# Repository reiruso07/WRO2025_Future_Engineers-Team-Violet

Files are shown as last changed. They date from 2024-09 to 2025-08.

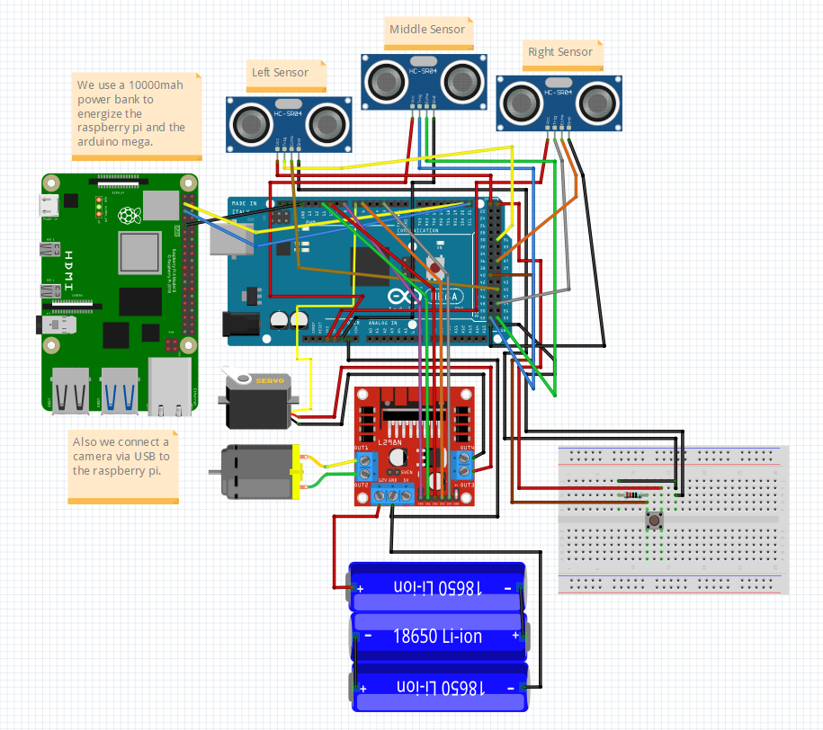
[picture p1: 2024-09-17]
schemes/scheme-structure/Full-Structure_Schematic.png

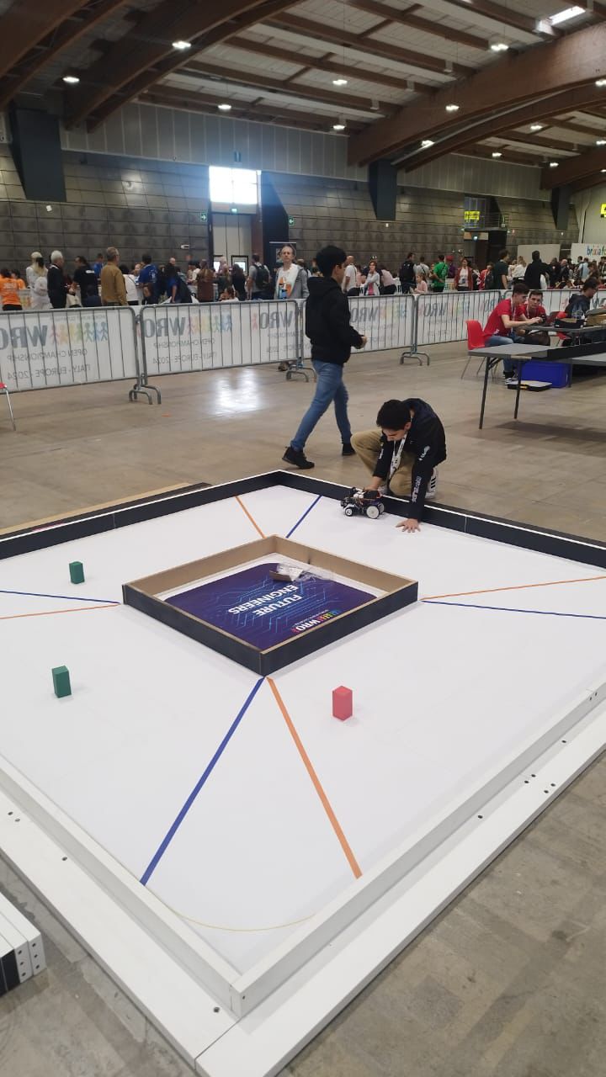
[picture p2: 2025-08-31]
t-photos/Our Journey/Italy_Competition_Test1.jpeg

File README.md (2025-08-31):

# Engineering Documentation - Team Violet 
Team Violet
## Introduction
In this repository you will find all the information related to the construction and assembly of the autonomous robot built by _Team Violet_ for the Future Engineers category in the 2025 Season.
This has been an incredible journey with a lot of obstacles, and we have done our best to come up with a design that we were not only satisfied with, but one that could properly acomplish all of the objectives present in this edition of the "Future Engineers" category.

## Contents
- [Team Violet's Members](https://github.com/reiruso07/WRO2025_Future_Engineers-Team-Violet/blob/main/README.md#team-violets-members)
- [Hardware Design](https://github.com/reiruso07/WRO2025_Future_Engineers-Team-Violet/blob/main/README.md#hardware-design)
   - [Design Process](https://github.com/reiruso07/WRO2025_Future_Engineers-Team-Violet/blob/main/README.md#design-process)
   - [Assembly Process](https://github.com/reiruso07/WRO2025_Future_Engineers-Team-Violet/blob/main/README.md#assembly-process)
   - [Elements](https://github.com/reiruso07/WRO2025_Future_Engineers-Team-Violet/blob/main/README.md#elements)
     - [3D Printed](https://github.com/reiruso07/WRO2025_Future_Engineers-Team-Violet/blob/main/README.md#3d-printed)
     - [Electronics](https://github.com/reiruso07/WRO2025_Future_Engineers-Team-Violet/blob/main/README.md#electronics)
- [Software Design](https://github.com/reiruso07/WRO2025_Future_Engineers-Team-Violet/blob/main/README.md#software-design)
   - [Image and Color Processing](https://github.com/reiruso07/WRO2025_Future_Engineers-Team-Violet/blob/main/README.md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)
     - [Image Capturing](https://github.com/reiruso07/WRO2025_Future_Engineers-Team-Violet/blob/main/README.md#image-capturing)
     - [Creating Red and Green masks](https://github.com/reiruso07/WRO2025_Future_Engineers-Team-Violet/blob/main/README.md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)
     - [Final Image](https://github.com/reiruso07/WRO2025_Future_Engineers-Team-Violet/blob/main/README.md#final-image)
     - [Distance from the cones](https://github.com/reiruso07/WRO2025_Future_Engineers-Team-Violet/blob/main/README.md#location-from-the-cones)
   - [Robot Movement](https://github.com/reiruso07/WRO2025_Future_Engineers-Team-Violet/blob/main/README.md#robot-movement)
     - [Smart Robot Servo configuration](https://github.com/reiruso07/WRO2025_Future_Engineers-Team-Violet/blob/main/README.md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)
     - [Robot Orientation](https://github.com/reiruso07/WRO2025_Future_Engineers-Team-Violet/blob/main/README.md#robot-orientation)
     - [Route Determination](https://github.com/reiruso07/WRO2025_Future_Engineers-Team-Violet/blob/main/README.md#route-determination)
   - [Data Sending](https://github.com/reiruso07/WRO2025_Future_Engineers-Team-Violet/blob/main/README.md#data-sending)
 - [Impact](https://github.com/reiruso07/WRO2025_Future_Engineers-Team-Violet/blob/main/README.md#impact)
 - [Our Journey](https://github.com/reiruso07/WRO2025_Future_Engineers-Team-Violet/blob/main/README.md#our-journey)

# Team Violet's Members
 - Adrian Alvarez:



>Hi, my name is Adrian Alvarez, I'm part of Team Violet and I'm responsible for the 3D designs used in the robot. My expectations of this competition are to learn and to test my skills in robotics.
 - Reinaldo Belmonte:



>My name is Reinaldo Belmonte. I am the team's programmer and I'm responsible for developing most (if not all) of the robot's moveset. My expectations for this season is to do my best with this project and, hopefully, end up in the first places.
 - Jose Zambrano:


   
>I am José Miguel Zambrano, the team's mechanic. I am in charge of the robot's assembly and its proper maintenance. For this season I hope, alongside my team, to deliver a project that meets the expectations, in addition to representing my institution and my country.

# Hardware Design
## Design Process
The robot is composed by a combination of 3D Printed parts for the most of its structure, the front wheels from a recicled toy car, the back wheels from a REV Robotics kit, and the electronics that give the robot its functionality.

Aditionally, the robot went through a multitude of changes until it reached its final iteration.
One of these changes was the replacement of the traditional DC motor that we used before with a «Hex Motor» , which provided a greater torque to the rear-wheel drive. 



As a result, the wheels used for the rear-wheel drive had to be also replaced, since the old ones couldn't adapt to the torque provided by the Hex Motor. This way we could take advantage of all the potential the Hex Motor had to offer.



Alongside the rear-wheel drive, we also made changes to the turning system, replacing the old Servomotor with a «Smart Robot Servo» , allowing for better and more precise turns when meeting a corner.



Another of these changes was the reorganization of its elements, given the changes in the motors used and the space they now occupied, we made a redistribution to most of the elements present in the robot, this time taking into account to make it even more accessible for repairs or adjustments to any of its parts.



The final design of the robot is intended as a modular design, consisting of 3 modules: lower «traction» module, middle «sensor processing» module, and upper «power supply and color processing» module. This makes it easier to make repairs on any of the modules or to replace or rearrange parts.



With all these changes made, a [3D design](https://github.com/reiruso07/WRO2024_Future_Engineers-Team-Violet/tree/main/other/model_structure) for the entire structure of the robot was made, thus facilitating its visualization and analysis.

## Assembly Process
The assembly process of the robot was divided into each module separately to later unify all the modules into a single robot. The assembly of the lower module started looking for different references on the internet to find an ideal location to place all the corresponding motors. After finding the ideal locations for each motor, the parts of the main chassis and the turning system were designed and 3D printed, tailored to each element to optimize the performance of the robot. 

Following this, we started the assembly of the second module, being much easier to carry out, since instead of using a 3d printed piece, we used a piece of compressed cardboard as a base to place all the elements of the second module. When performing this part of the assembly, we performed some functional tests to ensure that everything worked properly; there we realized that the HC-SR04 sensors suffered from detection failures due to how they were placed in the robot, so we designed an extension of the base to place them there, thus solving the problem.

Finally, we started the assembly of the 3rd and last module, following a sequence very similar to the previous one: We use a piece of compressed cardboard as the base of the 3rd module and place the corresponding elements.

And to unify the design, we drilled holes in the 3 bases of each module (except the main chassis which was already designed with these holes in mind) and joined them with multiple “pillar shafts” in a tower shape.

You can see the respective connections in the diagram below:

Team Violet (7)

## Elements
### 3D Printed
> [!NOTE]
> All of these pieces are printed in PLA plastic, with a thickness of 0.2mm and a filler level of between 20 to 50% (depends on the piece).

- **Main Chassis**: It's the piece that contains and supports all the components found in the robot.



- **Hex Motor Support Bracket**: A piece that helps fasten the Hex Motor to the Main Chassis structure.
  


- **Smart Robot Servo Support Bracket**: A piece that helps fasten the Servo Motor to the Main Chassis structure.



- **HC-SR04 Support Bracket**: Located in the "Bumper" piece, it serves as support for the HC-SR04 ultrasonic sensor, allowing it to function properly.
  


- **Bumper**: Used as a extension of the Main Chassis piece, it is used to locate the HC-SR04 sensors a little further ahead so it can detect the walls more easily.
  


- **Crossing System**: As it's name says, this part makes it possible to transmit the movement of the servomotor to the front wheels, thus allowing the robot to change direction.
  


- **Crossing System Support Piece**: The function of this piece is to join or support the two wheels, in other words, it is the one that produces a support point for them, which allows them to rotate on a fixed axle.



### Electronics
  -  **L298N Motor Driver**: Located in the middle module, it is used to manage the Hex Motor and provide both the Hex Motor and the Smart Robot Servo with energy.



> [!IMPORTANT]
> Specifications
>- Channels: 2 (supports 2 DC motors or 1 PAP motor)
>- Logic voltage: 5V.
>- Operating Voltage: 5V-35V.
>- Current consumption (Digital): 0 to 36mA.
>- Current capacity: 2A (peaks up to 3A).
>- Maximum power: 25W.
>- Weight: 30g.

  -  **Hex Motor**: Located in the lower module of the robot, this motor serves a rear wheel drive for the robot, providing the foward or backward motion of the robot.



> [!IMPORTANT]
>Specifications
>- Output Shaft: 5mm Female Hex
>- Weight: 199g.
>- Voltage: 12V DC
>- Free Speed: 125 RPM
>- Stall Torque: 3.2 N-m
>- Stall Current: 4.4 A
>- Gear Ratio: 72:1
>- Encoder Counts per Revolution
>- At the motor: 4 counts/revolution
>- At the output: 288 counts/revolution

  -   **Smart Robot Servo**: Located alongside the Hex Motor, it gives the robot the ability to rotate the front wheels, changing the orientation of the robot, thus allowing the robot to move freely in any direction on a flat surface.



> [!IMPORTANT]
>- Specifications
>- Weight: 58g.
>- Speed: 0.14 s/60° (at 6V)
>- Stall Torque: 13.5 kg-cm / 187.8 oz-in (at 6V)
>- Stall Current: 2A (at 6V)
>- Voltage Rating: 4.8V – 7.4V, 6V nominal
>- Input Pulse Range: 500μs – 2500μs
>- Default Angular Range: 270°
>- Maximum programmable range in angular mode: 280°
>- Gear Material: Metal
>- Spline type: 25T
>- Spline Internal Thread Size: M3
>- Spline Internal Thread Depth: 6mm

  -   **Arduino Mega 2560 R3**: Located in the middle module, it is used to manage the robot's mobility alongside the L298N Motor Driver, thus allowing the robot to move freely on a flat surface.



> [!IMPORTANT]
>- Microcontroller: ATmega2560
>- Input voltage: 7-12V.
>- 54 digital Input/Output pins (14 of them are PWM outputs).
>- 16 analog inputs.
>- 256k flash memory.
>- 16Mhz clock speed.

  -   **Raspberry Pi 4**: The Raspberry Pi 4 is a single-board development board used for entry-level computing. It is located in the upper module and it has the purpose of managing the "Color Processing" section, thus allowing the robot to recognize adjacent colors and use this information advantegiously.



> [!IMPORTANT]
>- Broadcom BCM2711, Quad core Cortex-A72 (ARM v8) 64-bit SoC @ 1.8GHz
>- 4GB LPDDR4-3200 SDRAM (depending on model)
>- 2.4 GHz and 5.0 GHz IEEE 802.11ac wireless, Bluetooth 5.0, BLE
>- Gigabit Ethernet
>- 2 USB 3.0 ports; 2 USB 2.0 ports.
>- 2 × micro-HDMI® ports (up to 4kp60 supported)
>- OpenGL ES 3.1, Vulkan 1.0
>- Micro-SD card slot for loading operating system and data storage
>- 5V DC via USB-C connector (minimum 3A*)
>- 5V DC via GPIO header (minimum 3A*)
>- Operating temperature: 0 – 50 degrees C ambient

   -   **HC-SR04 Ultrasonic Sensor**: The robot has 3 HC-SR04 ultrasonic sensors on the left, right and front of the "Bumper" piece, located in front of the middle module. They are used to provide orientation to the robot when moving in any environment, allowing it to detect obstacles or adjacent walls.



> [!IMPORTANT]
>- Supply voltage: 5 Vcc
>- Working frequency: 40 KHz
>- Maximum range: 4.5 m
>- Minimum range: 2.0 cm
>- Minimum trigger pulse duration (TTL level): 10 μS.
>- Duration of the output echo pulse (TTL level): 100-25000 μS.
>- Minimum waiting time between one measurement and the start of another: 20 mS.
  
   -   **Camera**: The robot uses an Spedal MF920P Webcam to recognize the colors in the environment. It has a Full HD 1080p resolution at 30 fps, with a H.264 Video Compression and a microphone incorporated.


   
   -   **3.7V 18650 Lithium Batteries**: Used to provide power to the Hex Motor and Smart Robot Servo on the lower module, this batteries have a nominal voltage of 3.7V and a maximum voltage of 4.2V and a capacity of 3500 mAh each.



   -   **LDNIO 10000mAh Power Bank**: We use a LDNIO 10000mAh Power Bank to supply Raspberry Pi and the Arduino Mega with energy. It has 1 USB ports, along with a Micro-USB port for charging, with an output voltage of 5V and 2.4A.



# Software Design
## Image and Color Processing
### Image Capturing
For color detection, the Spedal MF920P camera is used to capture a frame which is processed with Python thanks to the OpenCV image manipulation library.
### Creating Red and Green masks
OpenCV reads the images or frames in BGR, therefore it is necessary to transform them to the HSV color space. This is because the parameters that we are going to give to identify the colors work in the HSV model (Hue, Saturation, Value). To do this we will use the function `cv2.cvtColor`, as first argument we will give the image to transform, and then `cv2.COLOR_BGR2HSV`, to indicate that we will transform from BGR to HSV.
The parameters used to identify red were: 

    rojobajo1=np.array([0,150,20],np.uint8)

    rojoalto1=np.array([3,255,255],np.uint8)

    rojobajo2=np.array([175,100,20],np.uint8)

    rojoalto2=np.array([179,255,255],np.uint8)

and the parameters used for green were:
  
    verdebajo=np.array([35,100,20],np.uint8)

    verdealto=np.array([80,255,255],np.uint8)

The result of these procedures is a binary image in which the whites are the colors detected with the parameters given above. This image will be used later to obtain the final image.

Team Violet (1)

### Final Image
To obtain the final image we will use the functions `cv2.findContours` and `cv2.drawContours` from the OpenCV library. The function `cv2.findContours` is used to identify the colors detected in the binary image that together with the function `cv2.drawContours` is used to mark the obstacles in the final image.
### Location from the cones
To identify how far the cones are from the robot, the image is divided into four positions:

Team Violet (3)
1, 2, 3, and 4

The higher the position means that the obstacle is farther away from the robot, and with this information be able to calculate how much the robot has to move to avoid the cones more effectively.

## Robot Movement
### Smart Robot Servo configuration
The Smart Robot Servo is set on Pin 7 of the Arduino Mega and is configured with `Servo.write` function. The moveset of the Smart Robot Servo is defined by the distance given by the HC-SR04 sensors depending on whether the walls are near, far away or in a corner.
### Robot Orientation
The orientation of the robot is defined by the first corner, if the corner is of the rigth side it means that the direction is clockwise and 
vice versa.
### Route Determination
The determination of the routes is based on the color of the cone next to the robot. If the Python code detects a color this information will be sent to the arduino and transformed into a left or right turn depending on the detected color.

## Data Sending
First of all, we import the `smbus` library and then declare the `i2c identifier` that the Raspberry Pi 5 will have, additionally, the `i2c address` that the Raspberry Pi 5 has is placed, which is obtained thanks to a command executed in the terminal; then we create a function in charge of sending the information to the Arduino Mega 2560 R3 through an i2c connection that consist in three wires SDA (Serial Data Line), SCL (Serial Clock Line), and GND.

# Impact
The goal of this project is to evaluate the capabilities of the autonomous robot in fulfilling the various tasks that the competition demands. In the course of achieving these objectives, we had to develop a variety of skills to be able to meet all the objectives successfully, some of these skills being: the ability to analyze and correct errors in the programming of the project (both in the mobility section and in the color processing section), having to detect and correct these errors quickly in order to make progress in the expected completion times. Another of these skills was 3D design, which we used frequently to create different parts that were necessary to allow or facilitate the proper functioning of all components present in the robot.

The development of this project for the Future Engineers category was quite a journey to come up with a design that could stand up to the challenges we faced, and regardless of the outcome, it will be worth all the effort we made, since in the end, it made us grow.

# Our Journey
Our adventure in the WRO (World Robot Olympiad) began in 2023, when we were invited by our friends from Liceo Los Robles in Maracaibo. At first, it seemed like a simple task, but over time we discovered the true challenge of this competition, which has had a deep impact on us.

In 2024, we, José Miguel, Reinaldo, and Adrián joined forces in the Future Engineers category, embarking on a journey full of challenges and learning experiences. It was a roller coaster of emotions, with moments of triumph and frustration, but every second of effort has been worth it. The countless hours of work, discipline, and sacrifice have not only allowed us to grow in the field of robotics, but have also strengthened us as people. We have developed leadership, conflict resolution, decision-making, and, above all, a strong bond as a team.

2024 was a year of unforgettable achievements. We qualified for the national competition and, thanks to an invitation from Fundesteam Venezuela, we had the honor of participating in the WRO International Open in Brescia, Italy. Traveling to another continent to compete seemed like a dream, and we made it come true. We placed in an outstanding 4th place, just a few points behind the top spots. We were the only representatives from the Americas in our category and received a Gold mention for our performance, which placed us in first place in Latin America for the score achieved.
This experience filled us with pride and gratitude, but it also motivated us to seek new challenges in 2025. With a lot of effort, we have managed to qualify for the national finals among the top three teams. We are confident that our dedication and discipline will lead us to first place to represent Venezuela at the International Competition in Singapore.
Today, looking back, we feel immensely proud of how we have grown and overcome challenges together. We are ready to enjoy, cooperate, and give our best at this 2025 WRO National Competition.

--------------------------------------------------------------------------------------------------------------------------------------
Thank You. Team Violet - 2025.
======================================================================================================================================

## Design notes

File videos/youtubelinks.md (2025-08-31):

Team Violet (5)

## Demonstration Videos
### [- Standard Track, No Obstacles](https://youtu.be/GVMM1p4TWF8)
### [- Standard Track, Obstacles (Explanation)](https://youtu.be/eFcmwkvV04U)
### [- Standard Track, Obstacles 1](https://youtu.be/VMHjxnOMjBY)
### [- Standard Track, Obstacles 2](https://youtu.be/wLStcMTi5x4)
### [- Altered Track #1, No Obstacles](https://youtu.be/2meB4UbzeKI)
### [- Altered Track #2, No Obstacles](https://youtu.be/sTHwIlyS01U)
### [- Extra, How to cope with adversity](https://youtube.com/shorts/ftBgpBT6m5o?feature=share)

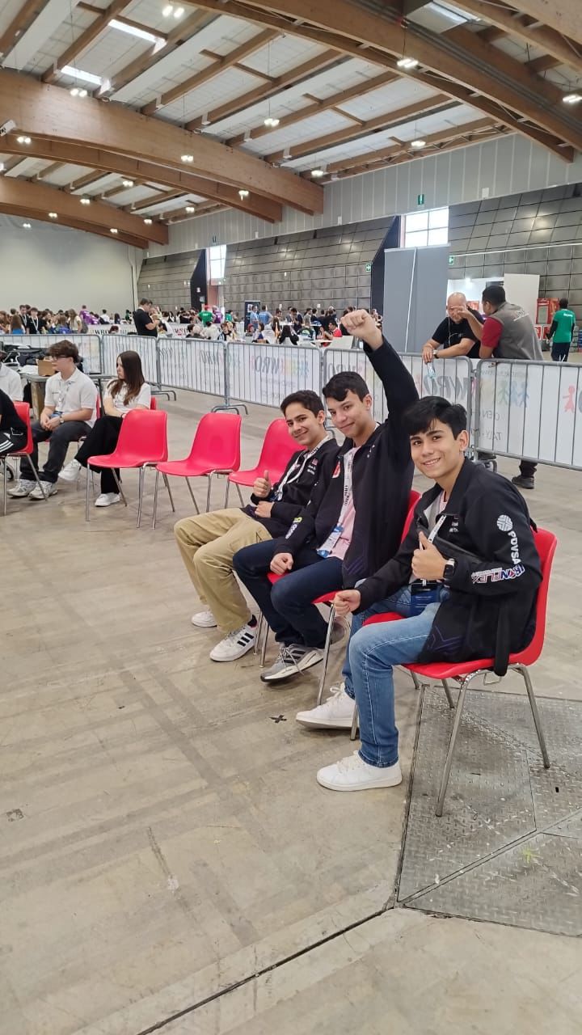
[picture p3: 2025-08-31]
t-photos/Our Journey/Italy_Competition1.jpeg

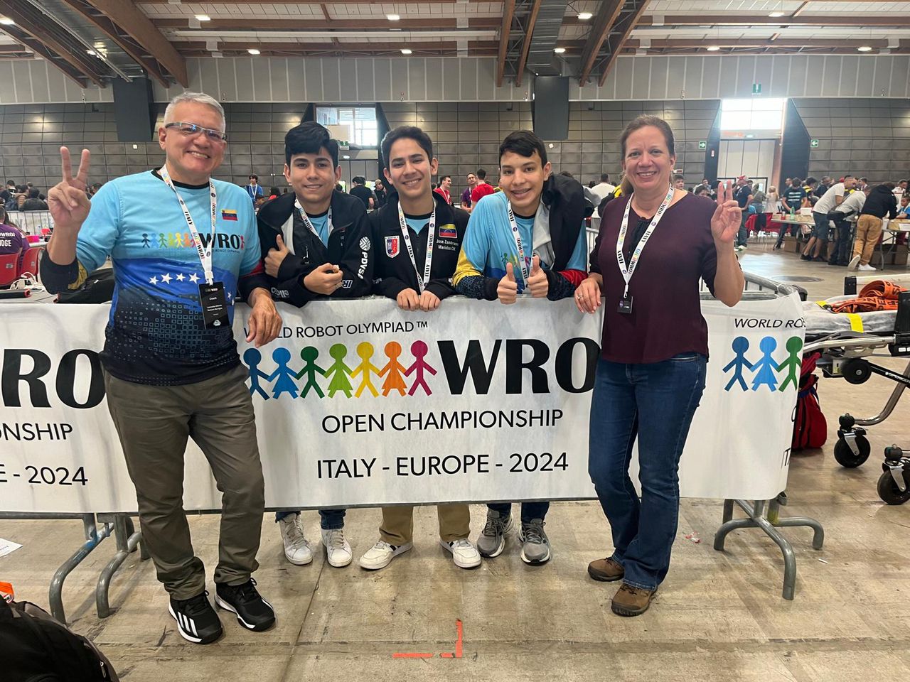
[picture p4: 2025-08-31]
t-photos/Our Journey/Italy_Competition3.jpeg

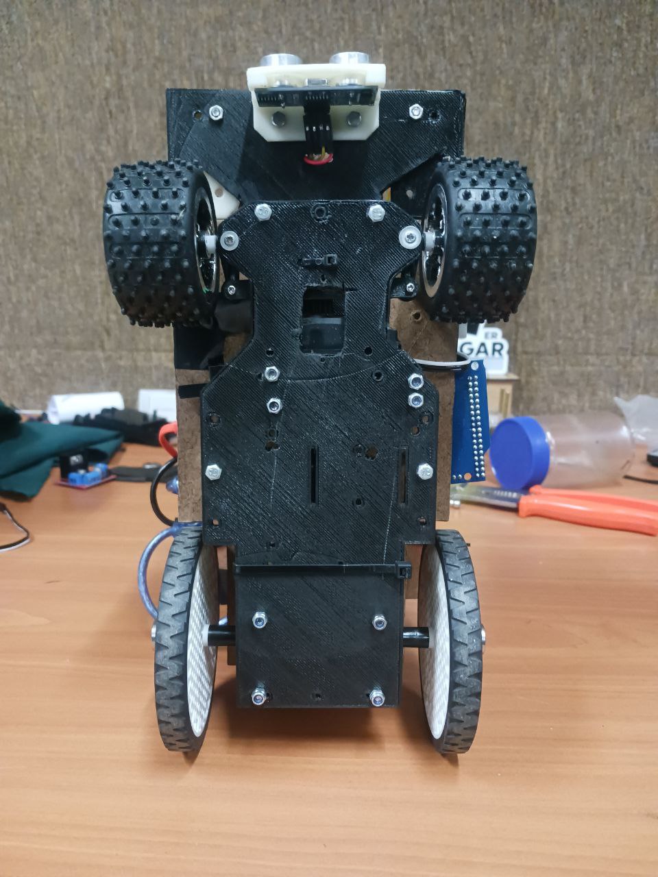
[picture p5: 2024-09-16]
v-photos/bottomview.jpg

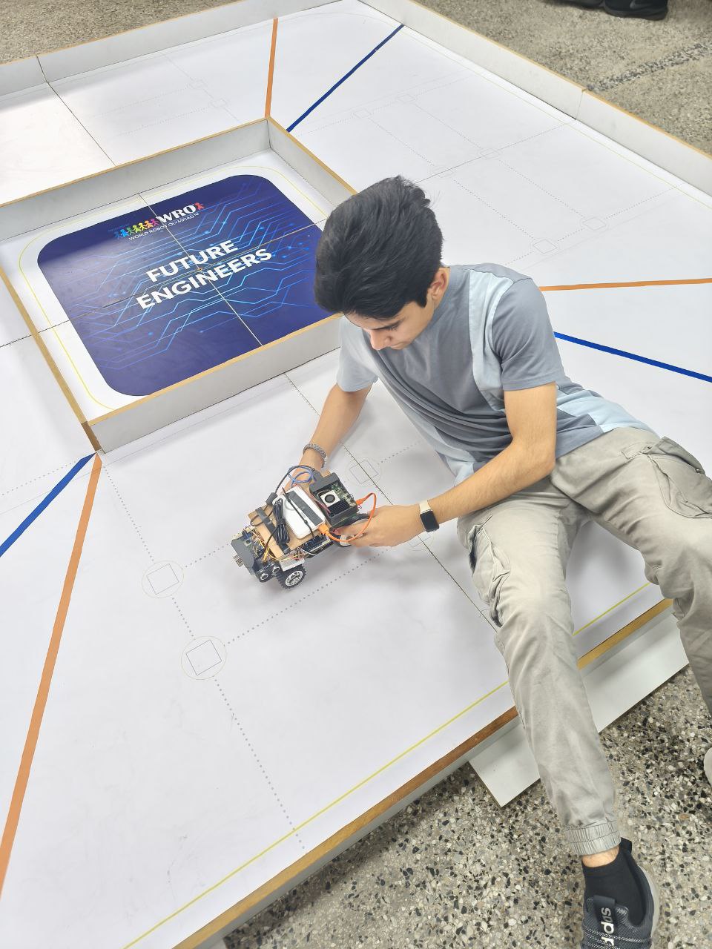
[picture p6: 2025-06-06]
t-photos/Teamwork/checking-robot.jpg

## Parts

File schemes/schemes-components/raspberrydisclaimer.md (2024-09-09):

> [!IMPORTANT]
> Since Raspberry Pi's are not "Open Hardware", and the 5 variant is so recent, we couldn't find the schematics for it. But we leave the Raspberry Pi 4 schematic since both have similar pinouts.

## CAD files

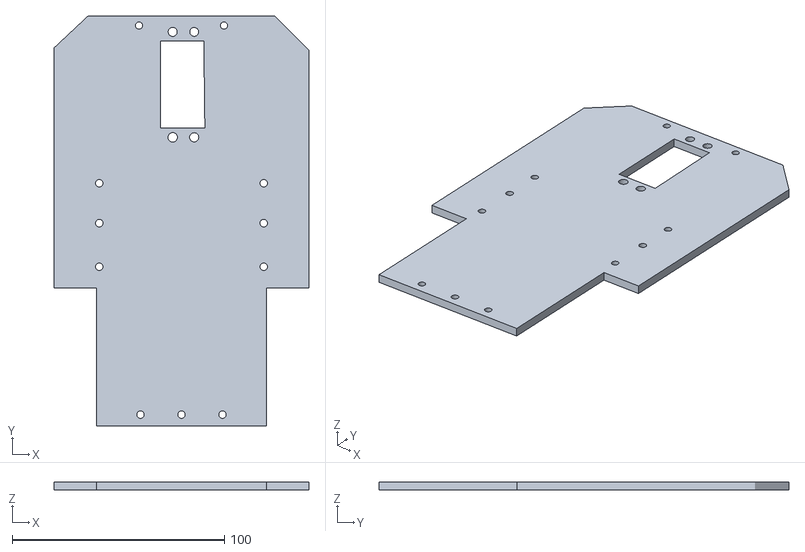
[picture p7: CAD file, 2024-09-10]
models/Main_Chassis_v1.stl
120.0 x 193.0 x 4.00

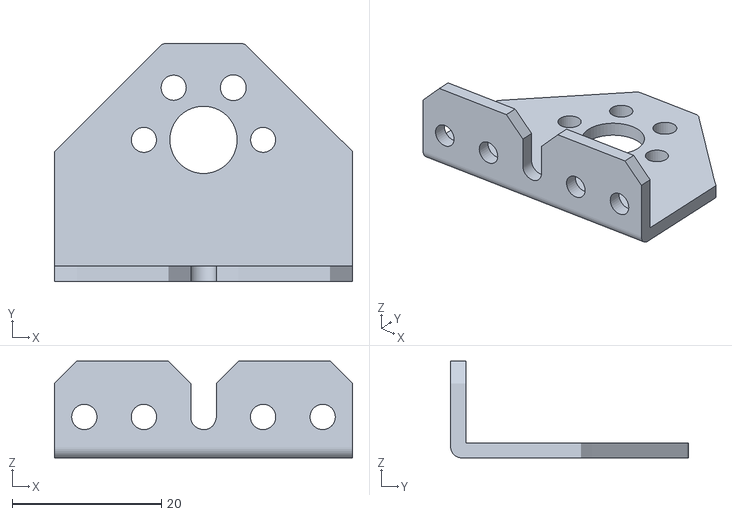
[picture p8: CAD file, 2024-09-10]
models/Core_Hex_Motor_Support_Bracket_v4.stl
40.0 x 31.9 x 13.0

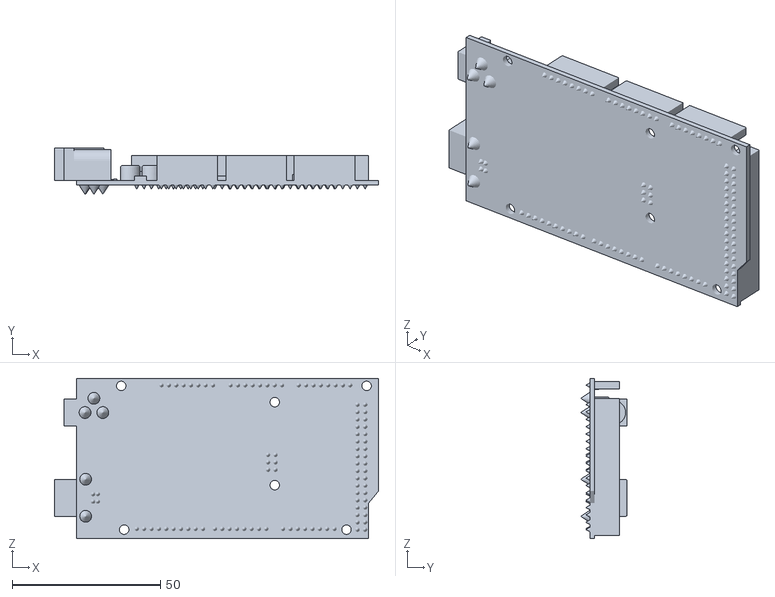
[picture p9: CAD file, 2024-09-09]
other/models-components/Arduino_Mega v1.stl
109.3 x 15.6 x 54.0

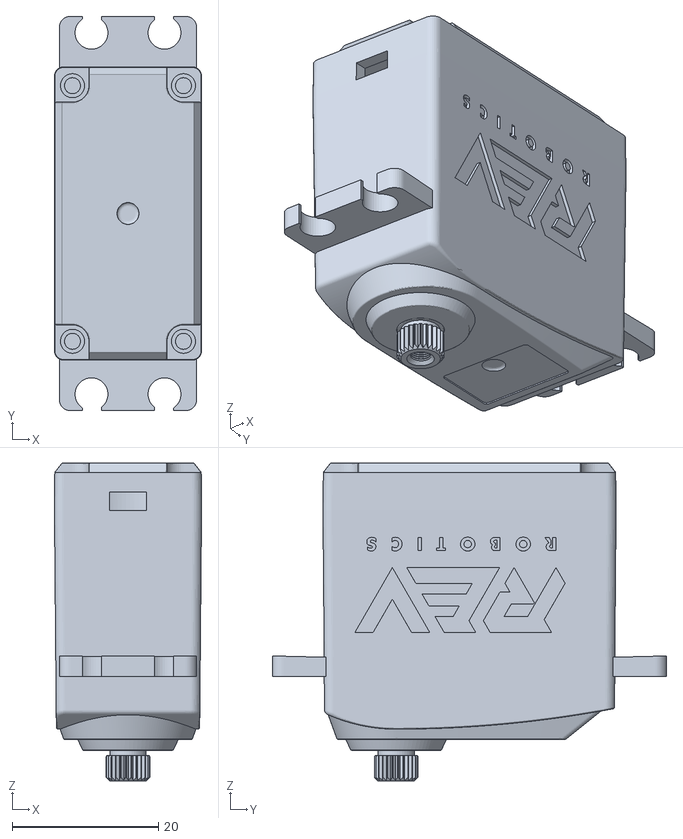
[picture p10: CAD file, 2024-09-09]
other/models-components/Smart Robot Servo.stl
20.2 x 54.0 x 43.5

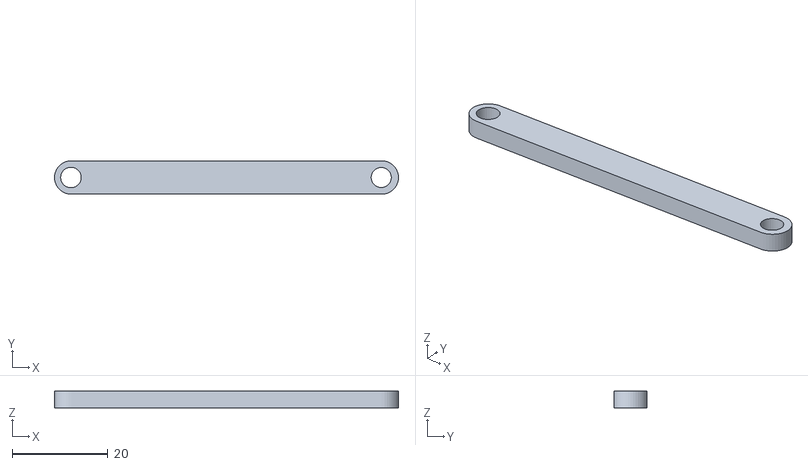
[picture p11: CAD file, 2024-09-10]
models/Crossing_Support_Piece_v2.1.stl
72.0 x 7.00 x 3.50

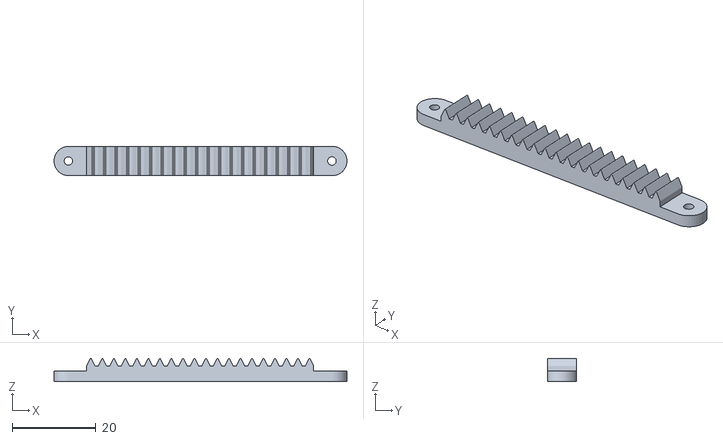
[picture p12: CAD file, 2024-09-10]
models/Crossing_System_Piece_v6.stl
70.0 x 7.00 x 5.56

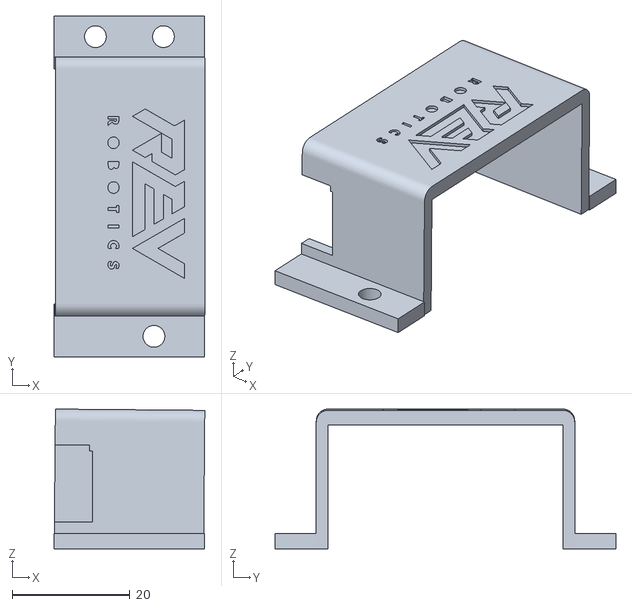
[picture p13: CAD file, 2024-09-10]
models/Smart_Servo_Support_Bracket_v2.stl
25.6 x 57.9 x 23.7

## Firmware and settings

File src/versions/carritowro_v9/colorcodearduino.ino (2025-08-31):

//Inclusion of Libraries
#include <Wire.h>
#include <Servo.h>
#include <L298N.h>
#include <NewPing.h>
//Variable declaration
#define IN2 10
#define IN1 11
#define IN3 6
#define IN4 3
#define I2C_DEVICE_ADDRESS 0x8
#define EN 8
String entradai2c="";
char te="";
int echo= 45;
int triger= 44;
int echo2=25;
int triger2=24;
int echo3=31;
int triger3=30;
int echo4=37;
int triger4=36;
int pulsador=40;
int maxd=450;
int atras=0;
int no=0;
int esq2=0,esq3=0;
int esqderatr=0;
int esquinadertrs=0;
int valorpulsador=0;
int esquinaderalt=0;
bool ra1,ra2,rm1,rm2,rm3,rm4,rm5,rm6,rm7,rm8,rm9,ra3,ra4,ra5,ra6,ra7,ra8,ra9,va1,va2,vm1,vm2,vm3,vm4,vm5,vm6,vm7,vm8,vm9,va3,va4,va5,va6,va7,va8,va9,rd1,rd2,rd3,rd4,rd5,rd6,rd7,rd8,rd9,vd1,vd2,vd3,vd4,vd5,vd6,vd7,vd8,vd9;
bool noconos,conorojoder,cnr,cnv;
int distanciaatr,distanciapasada;
int ciclo=0,vgn;
float distanciaade,distanciaizq,distanciader;
int cruzconorojo,cruzconorojoizq=0,cruzconorojoizq2=0,cruzconorojoizq3=0,cruzconorojonc=0,cruzconorojo2,cruzconoverde,cruzconoverde2=0,cuzconoverde3=0,cruzconoverdeizq,cruzconoverdeizq2=0,cuzconoverdeizq3=0;
int crucecono = 0,cruceconor2 = 0,cruceconocent=0,cruceconov=0,cruceconov2,cruceconovnc;
int esq=0;
int motors=1;
bool cnrojo=0,cnverde=0,rc=0,vc=0;
int lineas=0;
bool pared=0;
int paredizq=0;
int paredizqpeg=0;
int paredizqalt=0;
int paredder=0;
int paredderpeg=0;
int esquina=0,esquina2=0;
int esquinader=0,esquinader2=0,esquinader3=0;
bool esquinaderv=0,esquinaizqv=0;
bool esquinaizqr=0;
int pareder2=0;
int pared2=0;
int izq=0;
int der=0;
int esqc=0;
int si=0;
bool conorfin=0,conorcont=0,conovfin=0,conovcont=0,nc=0;
bool conorp=0,conovp=0,nconos;
int intervalocono = 1000,intervaloconov=1000;
int intervalodespuescono=1000;
const int intervalopared=200;
unsigned long cont;
unsigned long antespared=0;
unsigned long antesparedder=0;
unsigned long tiempoantesdelcont=0;
unsigned long tiempoantesdelcontder=0;
unsigned long valorantesconor = 0;
unsigned long valorantesconov = 0;
unsigned long valordespuesconor=0;
unsigned long valordespuesconov=0;
unsigned long contfincono=0,contfinconov=0;
unsigned long contnoconos=0;
int intervalo=2000;
int intervaloder=2200;
int esquinatrs=0;
//Motors and ultrasonics declaration
NewPing ultrasonidoade(triger,echo,maxd);
NewPing ultrasonidoder(triger3,echo3,maxd);
NewPing ultrasonidoizq(triger2,echo2,maxd);
NewPing ultrasonidoatr(triger4,echo4,maxd);
L298N motor(EN, IN2, IN1);
Servo servo;
void setup() {
  //Serial Monitor startup
  Serial.begin(115200);
  //I2c direction assignment
  Wire.begin(I2C_DEVICE_ADDRESS);
  Wire.onReceive(recibirm);
  Wire.onRequest(enviarM);
  //Servo pin assignment 
  servo.attach(39);
  //Definition of input and output pins
  pinMode(IN4, OUTPUT);
  pinMode(IN3, OUTPUT);
  pinMode(IN2, OUTPUT);
  pinMode(IN1, OUTPUT);
  pinMode(triger, OUTPUT);
  pinMode(echo, INPUT);
  pinMode(triger2, OUTPUT);
  pinMode(echo2, INPUT);
  pinMode(triger3, OUTPUT);
  pinMode(echo3, INPUT);
  pinMode(triger4, OUTPUT);
  pinMode(echo4, INPUT);
  pinMode(pulsador,INPUT_PULLUP);
  //Definition of motor speed
  motor.setSpeed(120);
  motor.stop();
  servo.write(90);
}
// principal loop start 
void loop() {
//Assignment of variable values
  cont = millis();
  distanciaade = ultrasonidoade.ping_cm();
  delay(30);
  distanciaizq = ultrasonidoizq.ping_cm();
  delay(30);
  distanciader = ultrasonidoder.ping_cm();
  delay(30);
  distanciaatr = ultrasonidoatr.ping_cm();
  if(lineas<12){
    digitalWrite(IN3,HIGH);
    digitalWrite(IN4,LOW);
  Serial.print("cont: ");
  Serial.println(cont);
  Serial.print("sensor adelante: ");
  Serial.println(distanciaade);
  Serial.print("sensor derecha: ");
  Serial.println(distanciader);
  Serial.print("sensor izquierda: ");
  Serial.println(distanciaizq);
  Serial.print("lineas");
  Serial.println(lineas);
  Serial.print("no: ");
  Serial.println(no);
  int centro=(distanciaizq+distanciader);
  if(motors==1){
    carrorect();
  }
  //Corner crossing conditions
  if((distanciaizq>100&&distanciaizq<300&&der==0&&izq==0&&distanciaade<=10&&si==0&&esquinadertrs==0&&esquinader==0&&esquinatrs==0)||esquina==1){
    if((cont-tiempoantesdelcont>intervalo)||esq==0){
      tiempoantesdelcont=cont;
      if(esq==0){
        noconos=0;
        ra1=0;
        ra2=0;
        ra3=0;
        ra4=0;
        ra5=0;
        ra6=0;
        ra7=0;
        ra8=0;
        ra9=0;
        rm1=0;
        rm2=0;
        rm3=0;
        rm4=0;
        rm5=0;
        rm6=0;
        rm7=0;
        rm8=0;
        rm9=0;
        rd1=0;
        rd2=0;
        rd3=0;
        rd4=0;
        rd5=0;
        rd6=0;
        rd7=0;
        rd8=0;
        rd9=0;
        va1=0;
        va2=0;
        va3=0;
        va4=0;
        va5=0;
        va6=0;
        va7=0;
        va8=0;
        va9=0;
        vm1=0;
        vm2=0;
        vm3=0;
        vm4=0;
        vm5=0;
        vm6=0;
        vm7=0;
        vm8=0;
        vm9=0;
        vd1=0;
        vd2=0;
        vd3=0;
        vd4=0;
        vd5=0;
        vd6=0;
        vd7=0;
        vd8=0;
        vd9=0;
        esquina=1;
        carrorect();
        stopcar();
        intervalo=1800;
        si=1;
        esq=1;
        servo.write(35);
        motor.backward(); 
        izq=1;
        motors=0;
      }
       else if(esq==1){
       stopcar();
       servo.write(85);
       motor.stop();
       motor.forward();
       intervalo=600;
       esq=2;
      }
      else if(esq==2){
        
       stopcar();
       servo.write(85);
       motor.stop();
       no=1;
       if(no==0){
          no=1;
       }
        intervalo=1000;
       esq=3;
      }
       else if(esq==3){
        carrorect();
        motors=1;
        lineas++;
        esquina=0;
        no=0;
        izq=1;
        enviarM();
        tiempoantesdelcont=0;
        esq=0;if(ra1==0&&ra2==0&&rm1==0&&rm2==0&&rd1==0&&rd2==0&&va1==0&&va2==0&&vm1==0&&vm2==0&&vd1==0&&vd2==0){
          noconos=1;
        }
        else{
          noconos=0;
        }
       }
       
  }
  }
 //Initial turn
if((distanciader>100&&esquina==0&&distanciaade<=15&&izq==0&&der==0&&si==0)||esquinader==1){
    if((cont-tiempoantesdelcont>intervaloder)||esq3==0){
      tiempoantesdelcont=cont;
      if(esq3==0){
        noconos=0;
        ra1=0;
        ra2=0;
        rm1=0;
        rm2=0;
        rd1=0;
        rd2=0;
        va1=0;
        va2=0;
        vm1=0;
        vm2=0;
        vd1=0;
        vd2=0;
        esquinader=1;
        carrorect();
        stopcar();
        intervaloder=1700;
        si=1;
        esq3=1;
        servo.write(140);
        motor.backward(); 
        der=1;
        motors=0;
      }
      else if(esq3==1){
        
       stopcar();
       servo.write(85);
       motor.stop();
       motor.forward();
       intervaloder=600;
       esq3=2;
      }
      else if(esq3==2){
        
       stopcar();
       servo.write(85);
       motor.stop();
       no=1;
       if(no==0){
          no=1;
       }
        intervaloder=1200;
       esq3=3;
      }
      else if(esq3==3){
        carrorect();
        motors=1;
        esq3=0;
        lineas++;
        no=0;
        if(no==1){
          no=0;
        }
        intervaloder=1000;
        esquinader=0;
        tiempoantesdelcont=0;
        si=1;
        enviarM();
        if(ra1==0&&ra2==0&&rm1==0&&rm2==0&&rd1==0&&rd2==0&&va1==0&&va2==0&&vm1==0&&vm2==0&&vd1==0&&vd2==0){
          noconos=1;
        }
        else{
          noconos=0;
        }
      }   
    }     
  }
  if((distanciader>100&&esquinadertrs==0&&esquinader3==0&&esquina==0&&distanciaade<=15&&izq==0&&der==1&&si==0&&cruzconorojo2==0&&conorfin==1&&conovfin==0)||esquinaderalt==1){
    Serial.println("esquina despues de esquivar cono rojo");
   if((cont-tiempoantesdelcont)>intervaloder||esq==0){
    tiempoantesdelcont=cont;
   Serial.println(tiempoantesdelcont); 
    if(esq==0){
      noconos=0;
        ra1=0;
        ra2=0;
        rm1=0;
        rm2=0;
        rd1=0;
        rd2=0;
        va1=0;
        va2=0;
        vm1=0;
        vm2=0;
        vd1=0;
        vd2=0;
        Serial.println("Hola");
        esquinaderalt=1;
        carrorect();
        stopcar();
        intervaloder=1900;
        si=1;
        esq=1;
        servo.write(140);
        motor.backward();
        motors=0;
      }
      else if(esq==1){
        no=1;
        if(no==0){
          no=1;
        }
       stopcar();
       servo.write(85);
       motor.stop();
        intervaloder=1200;
       esq=2;
      }
      else if(esq==2){
        carrorect();
        motors=1;
        esq=0;
        lineas++;
        no=0;
        intervaloder=1000;
        esquinaderalt=0;
        tiempoantesdelcont=0;
        enviarM();
        conorfin=0;
        if(ra1==0&&ra2==0&&rm1==0&&rm2==0&&rd1==0&&rd2==0&&va1==0&&va2==0&&vm1==0&&vm2==0&&vd1==0&&vd2==0){
          noconos=1;
        }
        else{
          noconos=0;
        }
      }   
        
   }
  }
  if((distanciader>100&&distanciaade<=36&&izq==0&&der==1&&si==0&&cruzconorojo2==0&&conovfin==1&&conorfin==0)||esquinaderv==1){
   if((cont-tiempoantesdelcont)>intervaloder||esq==0){
    tiempoantesdelcont=cont;
    if(esq==0){
      noconos=0;
        ra1=0;
        ra2=0;
        rm1=0;
        rm2=0;
        rd1=0;
        rd2=0;
        va1=0;
        va2=0;
        vm1=0;
        vm2=0;
        vd1=0;
        vd2=0;
        esquinaderv=1;
        carrorect();
        stopcar();
        intervaloder=1200;
        si=1;
        esq=1;
        servo.write(85);
       motor.backward();
        motors=0;
      }
      
      else if(esq==1){
       stopcar();
       
       servo.write(30);
        motor.forward();
        intervaloder=1800;
       esq=2;
      }
      else if(esq==2){
        no=1;
        if(no==0){
          no=1;
        }
        
       stopcar();
       no=1;
       servo.write(85);
       motor.stop();
        intervaloder=1200;
       esq=3;
      }
      else if(esq==3){
        carrorect();
        motors=1;
        esq=0;
        lineas++;
        no=0;
        intervaloder=1000;
        esquinaderv=0;
        tiempoantesdelcont=0;
        enviarM();
        conovp=0;
        conorp=0;
        conovfin=0;
        if(ra1==0&&ra2==0&&rm1==0&&rm2==0&&rd1==0&&rd2==0&&va1==0&&va2==0&&vm1==0&&vm2==0&&vd1==0&&vd2==0){
          noconos=1;
        }
        else{
          noconos=0;
        }
      }   
        
   }
  }
  if((distanciaizq>100&&distanciaade<=15&&izq==1&&der==0&&si==0&&cruzconorojo2==0&&conorfin==1&&conovfin==0)||esquinaizqr==1){
    tiempoantesdelcont=cont;
    if(esq==0){
      noconos=0;
        ra1=0;
        ra2=0;
        rm1=0;
        rm2=0;
        rd1=0;
        rd2=0;
        va1=0;
        va2=0;
        vm1=0;
        vm2=0;
        vd1=0;
        vd2=0;
        esquinaizqr=1;
        carrorect();
        stopcar();
        intervaloder=1800;
        si=1;
        esq=1;
        servo.write(85);
       motor.backward();
        motors=0;
      }
      
      else if(esq==1){
       stopcar();
       
       servo.write(140);
        motor.forward();
        intervaloder=1600;
       esq=2;
      }
      else if(esq==2){
       stopcar();
       no=1;
       servo.write(85);
       motor.backward();
        intervaloder=600;
       esq=3;
      }
      else if(esq==3){
        no=1;
        if(no==0){
          no=1;
        }
        Serial.println("se detuvo");
       stopcar();
       no=1;
       servo.write(85);
       motor.stop();
        intervaloder=1200;
       esq=4;
      }
      else if(esq==4){
        carrorect();
        motors=1;
        esq=0;
        lineas++;
        no=0;
        intervaloder=1000;
        esquinaizqr=0;
        tiempoantesdelcont=0;
        enviarM();
        conorfin=0;
        conovp=0;
        conorp=0;
        if(ra1==0&&ra2==0&&rm1==0&&rm2==0&&rd1==0&&rd2==0&&va1==0&&va2==0&&vm1==0&&vm2==0&&vd1==0&&vd2==0){
          noconos=1;
        }
        else{
          noconos=0;
        }
      }   
        
   }
  }
  if((distanciaizq>100&&esquinadertrs==0&&esquinader3==0&&esquina==0&&distanciaade<=15&&izq==1&&der==0&&si==0&&cruzconorojo2==0&&conovfin==1&&conorfin==0)||esquinaizqv==1){
    Serial.println("esquina despues de esquivar cono verde anti horario");
   if((cont-tiempoantesdelcont)>intervaloder||esq==0){
    tiempoantesdelcont=cont;
   Serial.println(tiempoantesdelcont); 
    if(esq==0){
      noconos=0;
        ra1=0;
        ra2=0;
        rm1=0;
        rm2=0;
        rd1=0;
        rd2=0;
        va1=0;
        va2=0;
        vm1=0;
        vm2=0;
        vd1=0;
        vd2=0;
        Serial.println("Hola");
        esquinaizqv=1;
        carrorect();
        stopcar();
        intervaloder=1700;
        si=1;
        esq=1;
        servo.write(30);
        motor.backward();
        motors=0;
      }
      
      else if(esq==1){
       stopcar();
       servo.write(85);
       motor.backward();
        intervaloder=300;
       esq=2;
      }
      else if(esq==2){
       stopcar();
       no=1;
       if(no==0){
        no=1;
       }
       servo.write(85);
       motor.stop();
        intervaloder=1200;
       esq=3;
      }
      else if(esq==3){
        carrorect();
        motors=1;
        esq=0;
        lineas++;
        no=0;
        intervaloder=1000;
        esquinaizqv=0;
        tiempoantesdelcont=0;
        enviarM();
        conovfin=0;
        if(ra1==0&&ra2==0&&rm1==0&&rm2==0&&rd1==0&&rd2==0&&va1==0&&va2==0&&vm1==0&&vm2==0&&vd1==0&&vd2==0){
          noconos=1;
        }
        else{
          noconos=0;
        }
      }   
        
   }
  }
  //Obstacle avoiding conditions
  if((((ra1!=0||ra2!=0)||cruzconorojoizq==1)&&der==0&&izq==1)&&esquinaizqr==0&&esquinaizqv==0&&esquinaderv==0&&esquina==0&&esquina2==0&&esq==0){
    Serial.println("cono rojo izq");
    noconos=0;
    if((((cont-valorantesconor)>intervalocono)||crucecono==0)&&cnrojo==0){
      valorantesconor=cont;
      if(crucecono==0){
          intervalocono=900;
          Serial.println("Hola b1");
         crucecono=1;
        cruzconorojoizq=1;
        carroesqder();
        motors=0;
        
        }
        else if(crucecono==1){
          Serial.println("Hola b2");
         crucecono=2;
         motor.stop();
         carroesqizq();
         intervalocono=1000;
        }
        else if(crucecono==2){
          Serial.println("Hola b3");
        crucecono=0;
        carrorect();
        valorantesconor=0;
        intervalocono=900;
        cnrojo=1;
        if(cnrojo==0){
          cnrojo=1;
        }
        crucecono=0;
        
        }
    }
    if(cnrojo==1){
      Serial.println("mantenerse derecho");
      
     if(((((cont-contfincono)>=1000)&&conorcont==1)||rc==1)&&cnr==0){
          Serial.println("centrar adios cono 3");
          
          if(((cont-valordespuesconor)>intervalodespuescono)||vgn==0){
            Serial.println("Hola mundo");
            valordespuesconor=cont;
        if(vgn==0){
          carrorect();
          motor.stop();
          no=1;
          rc=1;
          vgn=1;
          ciclo=1;
          
        }
        else if(vgn==1&&(vd1!=0||vd2!=0)){
          Serial.println("pp");
          no=0;
          cruzconorojoizq=0;
          crucecono=0;
          ra1=0;
          ra2=0;
          cnrojo=0;
          conorcont=0;
          valordespuesconor=0;
          vgn=0;
          rc=0;
          conorp=1;
          conorfin=0;
        }
        else if(vgn==1&&(vd1==0&&vd2==0)){
          Serial.println("ii");
          carrorect();
          cnr=1;
          conorcont=0;
          valordespuesconor=0;
          conorp=0;
          conorcont=0;
          no=0;
          ciclo=0;
        }
        
     }
    
     
    }
  
     else if(distanciaade<=100&&(((cont-contfincono)>=1000)&&conorcont==1)&&cnr==1){
      carrorect();
        cruzconorojoizq=0;
        crucecono=0;
        ra1=0;
        ra2=0;
        ra3=0;
        ra4=0;
        ra5=0;
        ra6=0;
        ra7=0;
        ra8=0;
        ra9=0;
        rm1=0;
        rm2=0;
        rm3=0;
        rm4=0;
        rm5=0;
        rm6=0;
        rm7=0;
        rm8=0;
        rm9=0;
        rd1=0;
        rd2=0;
        rd3=0;
        rd4=0;
        rd5=0;
        rd6=0;
        rd7=0;
        rd8=0;
        rd9=0;
        motors=1;
        cnrojo=0;
        conorfin=1;
        conorp=1;
        conorcont=0;
        rc=0;
        si=0;
     }
     else{
      if(conorcont==0){
        Serial.println("cont activated");
        contfincono=cont;
        conorcont=1;
      }
       conorojo();
        motors=0;
     }
    }
  }
  if((((rd1!=0||rd2!=0)||cruzconorojonc==1)&&der==0&&izq==1&&nc==1)&&esquinaizqr==0&&esquinaizqv==0&&esquinaderv==0&&esquina==0&&esquina2==0&&esq==0){
    noconos=0;
    if((((cont-valorantesconor)>intervalocono)||crucecono==0)&&cnrojo==0){
      valorantesconor=cont;
      if(crucecono==0){
          intervalocono=900;
         crucecono=1;
        cruzconorojonc=1;
        carroesqder();
        motors=0;
        
        }
        else if(crucecono==1){
         crucecono=2;
         motor.stop();
         carroesqizq();
         intervalocono=1100;
        }
        else if(crucecono==2){
        crucecono=0;
        carrorect();
        valorantesconor=0;
        intervalocono=900;
        cnrojo=1;
        nc=0;
        ciclo=0;
        si=0;
        cruzconorojonc=0;
        conorfin=1;
        rd1=0;
        rd2=0;
        rd3=0;
        rd4=0;
        rd5=0;
        rd6=0;
        rd7=0;
        rd8=0;
        rd9=0;
        if(cnrojo==0){
          cnrojo=1;
        }
        crucecono=0;
        
        }
    }
  }
    if((((rm1!=0||rm2!=0)||cruzconorojo2==1)&&der==0&&izq==1)&&esquinaizqr==0&&esquinaizqv==0&&esquinaderalt==0&&esquinaderv==0&&esquina==0&&va2==0&&va1==0&&ra2==0&&ra1==0){
    noconos=0;
    if((((cont-valorantesconor)>intervalocono)||cruceconocent==0)&&cnrojo==0){
      valorantesconor=cont;
      if(cruceconocent==0){
          intervalocono=1000;
         cruceconocent=1;
        cruzconorojo2=1;
        carroesqder();
        motors=0;
        }
        else if(cruceconocent==1){
          motors=0;
         cruceconocent=2;
         motor.stop();
         servo.write(145);
         motor.forward();
         valorantesconor=cont;
         intervalocono=1000;
        }
        else if(cruceconocent==2){
        cruceconocent=0;
        carrorect();
        valorantesconor=0;
        intervalocono=800;
        cnrojo=1;
        crucecono=0;
        conorfin=1;
        
        }
    }
    if(cnrojo==1){
      
     if((distanciaade<=100&&((cont-contfincono)>=2000)&&conorcont==1)){
        carrorect();
        cruzconorojo2=0;
        crucecono=0;
        cruceconocent=0;
        rm1=0;
        rm2=0;
        rm3=0;
        rm4=0;
        rm5=0;
        rm6=0;
        rm7=0;
        rm8=0;
        rm9=0;
        motors=1;
        cnrojo=0;
        conorfin=1;
        paredder=0;
       pareder2=0;
       motors=1;
       paredizq=0;
      si=0;
      pared2=0;
      conorcont=0;
     }
     else{
      if(conorcont==0){
        contfincono=cont;
        conorcont=1;
      }
       conorojo();
        motors=0;
     }
    }
  }
  else if((rm1!=0||rm2!=0)&&vd1==1||vd2==1||va1==1||va2==1||ra2==1||ra1==1||rd1==1||rd2==1){
    rm1=0;
        rm2=0;
        cruzconorojo2=0;
  }
  if((((rd1!=0||rd2!=0)||cruzconorojoizq3==1)&&der==0&&izq==1&&conovp==1)&&esquinader==0&&esquinader2==0&&esquinaderalt==0&&esquinaderv==0){
    noconos=0;
    if((((cont-valorantesconor)>intervalocono)||cruceconor2==0)){
      valorantesconor=cont;
      if(cruceconor2==0){
          intervalocono=1200;
         cruzconorojoizq3=1;
         cruceconor2=1;
        carroesqder();
        motors=0;
        }
        else if(cruceconor2==1){
          motors=0;
         cruceconor2=2;
         motor.stop();
         carrorect();
         servo.write(145);
         intervalocono=1500;
        }
        else if(cruceconor2==2){
        carrorect();
        valorantesconor=0;
        cruceconor2=0;
        intervalocono=1500;
        cruzconorojoizq3=0;
        conorfin=1;
        rd1=0;
        rd2=0;
        rd3=0;
        rd4=0;
        rd5=0;
        rd6=0;
        rd7=0;
        rd8=0;
        rd9=0;
        ciclo=0;
        si=0;
        }
    }
  }
  //Red obstacle in front
  if((((ra1!=0||ra2!=0)||cruzconorojo==1)&&der==1&&izq==0&&conorp==0)&&esquinader==0&&esquinader2==0&&esquinaderalt==0&&esquinaderv==0&&esquina==0&&esquina2==0){
    noconos=0;
    if((((cont-valorantesconor)>intervalocono)||crucecono==0)&&cnrojo==0){
      valorantesconor=cont;
      if(crucecono==0){
          intervalocono=900;
         crucecono=1;
        cruzconorojo=1;
        carroesqder();
        motors=0;
        }
        else if(crucecono==1){
         crucecono=2;
         motor.stop();
         carroesqizq();
         intervalocono=900;
        }
        else if(crucecono==2){
        crucecono=0;
        carrorect();
        valorantesconor=0;
        intervalocono=900;
        cnrojo=1;
        if(cnrojo==0){
          cnrojo=1;
        }
        crucecono=0;
        }
        
    }
    if(cnrojo==1){
      
     if(((((cont-contfincono)>=1500)&&conorcont==1)||rc==1)&&cnr==0){
          
          if(((cont-valordespuesconor)>intervalodespuescono)||vgn==0){
            valordespuesconor=cont;
        if(vgn==0){
          carrorect();
          motor.stop();
          no=1;
          rc=1;
          
          vgn=1;
          ciclo=1;
        }
        else if(vgn==1&&(vd1!=0||vd2!=0)){
          no=0;
          cruzconorojo=0;
          crucecono=0;
          ra1=0;
          ra2=0;
          cnrojo=0;
          conorcont=0;
          valordespuesconor=0;
          vgn=0;
          rc=0;
          conorp=1;
          conorcont=0;
          conorfin=0;
        }
        else if(vgn==1&&(vd1==0&&vd2==0)){
          carrorect();
          cnr=1;
          conorcont=0;
          valordespuesconor=0;
          conorp=0;
          conorcont=0;
          no=0;
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

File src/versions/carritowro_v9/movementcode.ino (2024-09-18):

//Inclusion of Libraries
#include <Servo.h>
#include <L298N.h>
#include <NewPing.h>
//Variable declaration
int IN2= 10;
int IN1= 11;
int IN3= 6;
int IN4= 3;
int EN= 8;
int echo= 53;
int triger= 52;
int echo2=45;
int triger2=31;
int echo3=37;
int triger3=49;
int buzz=11;
int maxd=450;
int atras=0;
int no=0;
int esq2=0;
int esqderatr=0;
int esquinadertrs=0;
int esquina=0;
int esq=0;
int motors=1;
int lineas=0;
bool pared=0;
int paredizq=0;
int paredizqpeg=0;
int paredizqalt=0;
int paredder=0;
int paredderpeg=0;
int paredderalt=0;
bool pareder=0;
int esquinader=0;
int pareder2=0;
int pared2=0;
int izq=0;
int der=0;
int si=0;
const int intervalopared=200;
unsigned long antespared=0;
unsigned long antesparedder=0;
unsigned long tiempoantesdelcont=0;
unsigned long tiempoantesdelcontder=0;
const  int intervalo=2000;
const int intervaloatr=1850;
const int intervaloder=1900;
const int intervaloderatr=1800;
int esquinatrs=0;
//Motors and ultrasonic declaration
Servo servo;
NewPing ultrasonidoade(triger,echo,maxd);
NewPing ultrasonidoder(triger3,echo3,maxd);
NewPing ultrasonidoizq(triger2,echo2,maxd);
L298N motor(EN, IN2, IN1);

void setup() {
  //Serial monitor startup
  Serial.begin(9600);
  //Servo pin assignment
  servo.attach(7);
  //Definition of input and output pins
  pinMode(IN4, OUTPUT);
  pinMode(IN3, OUTPUT);
  pinMode(IN2, OUTPUT);
  pinMode(IN1, OUTPUT);
  pinMode(triger, OUTPUT);
  pinMode(echo, INPUT);
  pinMode(triger2, OUTPUT);
  pinMode(echo2, INPUT);
  pinMode(triger3, OUTPUT);
  pinMode(echo3, INPUT);
  pinMode(buzz,OUTPUT);
  //Definition of motor speed
  motor.setSpeed(120);
  motor.stop();
  servo.write(90);
  
}

void loop() {
  //Loop start
  if(lineas<12){
    digitalWrite(IN3,HIGH);
    digitalWrite(IN4,LOW);
  //Assignment of variable values
  unsigned long cont = millis();
  float distanciaade = ultrasonidoade.ping_cm();
  float distanciaizq = ultrasonidoizq.ping_cm();
  float distanciader = ultrasonidoder.ping_cm();

  }
  if(motors==1){
    carrorect();
  }
//Corner crossing conditions
if((distanciaizq>100&&distanciaizq<300&&der==0&&izq==0&&si==0&&no==0&&esquinadertrs==0&&esquinader==0&&esquinatrs==0&&distanciaade>50&&distanciaade<80)||esquina==1){
    if((cont-tiempoantesdelcont>intervalo)||esq==0){
      tiempoantesdelcont=cont;
      if(esq==0&&esquinadertrs==0){
        esquina=1;
        si=1;
        no=1;
        esq=1;
        carroesqizq();
        motors=0;
        izq=1;
      }
      else{
        esq=0;
        carrorect();
        esquina=0;
        motors=1;
        lineas++;
        tiempoantesdelcont=0;
      }
    }
  }
if((distanciaizq>100&&distanciaizq<300&&izq==1&&der==0&&si==0&&no==0&&esquinadertrs==0&&esquinader==0&&esquinatrs==0&&distanciaade>50&&distanciaade<80)||esquina==1){
    if((cont-tiempoantesdelcont>intervalo)||esq==0){
      tiempoantesdelcont=cont;
      if(esq==0&&esquinadertrs==0){
        esquina=1;
        si=1;
        no=1;
        esq=1;
        carroesqizq();
        motors=0;
        izq=1;
      }
      else{
        esq=0;
        carrorect();
        esquina=0;
        motors=1;
        lineas++;
        tiempoantesdelcont=0;
      }
    }
  }
if((distanciaizq>=100&&distanciaizq<=300&&esquinadertrs==0&&esquinader==0&&esquina==0&&izq==0&&der==0&&si==0&&no==0&&distanciaade<=50)||esquinatrs==1){
    if((cont-tiempoantesdelcont>intervaloatr)||esq2==0){
      tiempoantesdelcont=cont;
      if(esq2==0&&esquinadertrs==0){
        esquinatrs=1;
        si=1;
        esq2=1;
        carroesqizq2();
        motors=0;
        izq=1;
        no=1;
      }
      else if(esq2==1&&esquinadertrs==0){
        esq2=0;
        carrorect();
        esquinatrs=0;
        motors=1;
        lineas++;
        tiempoantesdelcont=0;
      }
    }
  } 
if((distanciaizq>=100&&distanciaizq<=300&&esquinadertrs==0&&esquinader==0&&esquina==0&&izq==1&&der==0&&si==0&&no==0&&distanciaade<=50)||esquinatrs==1){
    if((cont-tiempoantesdelcont>intervaloatr)||esq2==0){
      tiempoantesdelcont=cont;
      if(esq2==0&&esquinadertrs==0){
        esquinatrs=1;
        si=1;
        esq2=1;
        carroesqizq2();
        motors=0;
        izq=1;
        no=1;
      }
      else if(esq2==1&&esquinadertrs==0){
        esq2=0;
        carrorect();
        esquinatrs=0;
        motors=1;
        lineas++;
        tiempoantesdelcont=0;
      }
    }
  } 
if((distanciader>100&&distanciader<300&&esquinadertrs==0&&esquinatrs==0&&esquina==0&&distanciaade>50&&distanciaade<80&&izq==0&&der==0&&si==0&&no==0)||esquinader==1){
    if((cont-tiempoantesdelcont>intervaloder)||esq==0){
      tiempoantesdelcont=cont;
      if(esq==0&&esquinadertrs==0){
        esquinader=1;
        si=1;
        esq=1;
        carroesqder();
        motors=0;
        der=1;
        no=1;
      }
      else{
        esq=0;
        carrorect();
        esquinader=0;
        motors=1;
        lineas++;
        tiempoantesdelcont=0;
      }
    }
  }
if((distanciader>100&&distanciader<300&&esquinadertrs==0&&esquinatrs==0&&esquina==0&&distanciaade>50&&distanciaade<80&&izq==0&&der==1&&si==0&&no==0)||esquinader==1){
    if((cont-tiempoantesdelcont>intervaloder)||esq==0){
      tiempoantesdelcont=cont;
      if(esq==0&&esquinadertrs==0){
        esquinader=1;
        si=1;
        esq=1;
        carroesqder();
        motors=0;
        der=1;
        no=1;
      }
      else{
        esq=0;
        carrorect();
        esquinader=0;
        motors=1;
        lineas++;
        tiempoantesdelcont=0;
      }
    }
  }
if((distanciader>100&&distanciader<300&&esquinader==0&&esquinatrs==0&&esquina==0&&izq==0&&der==0&&si==0&&no==0&&distanciaade<=50)||esquinadertrs==1){
    if((cont-tiempoantesdelcontder>intervaloderatr)||esqderatr==0){
      tiempoantesdelcontder=cont;
      if(esqderatr==0){
        esquinadertrs=1;
        si=1;
        esqderatr=1;
        carroesqder2();
        motors=0;
        der=1;
        no=1;
      }
      else if(esqderatr==1){
        esqderatr=0;
        carrorect();
        esquinadertrs=0;
        motors=1;
        lineas++;
        tiempoantesdelcont=0;
      }
    }
  }
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

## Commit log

2024-05-16 Added 3D Models
    [(P.T.S.T.I.D.K.W.I.C) piece_for_the_turning_system_that_i_dont_know_what_its_called.stl, chassis.stl, gimbal.stl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]
2024-05-16 Added Schematics
